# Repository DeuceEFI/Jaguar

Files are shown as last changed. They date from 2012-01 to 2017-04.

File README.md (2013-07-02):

# Jaguar Board for FreeEMS

JAG 07/02/2013 1157 EDT (GMT-0400)

####Do NOT use these files in the dev branch to make a PCB, the 0.6-alpha PCB has not been tested.  See the TODO.md file for the up to date changes from the 0.4-alpha to the 0.6-alpha board.  The 0.5-alpha was a commit of gerber files after I noticed that the traces were incorrect to the AAP and MAP sensors, it was never manufactured.

### Introduction

The name "Jaguar" comes from my initials and the great cat, keeping in the FreeEMS tradition of using cat names for hardware...  The aim of the Jaguar project is to create a hardware solution for FreeEMS that caters to the needs of the General Motors 4/6/8 cylinder engines running either an electronic advance distributor or wasted spark DIS system.  The Jaguar board can also be used for other 4/6/8 cylinder engines using a Ford EDIS ignition system.  The TC442xA Ignitor Drivers specified in the Bill of Materials can be used as logic level outputs to the logic level inputs on EDIS/DIS modules or to directly drive 12v ignitors. 

Please see forum.diyefi.org for the most up to date information and links for this project and all of the other aspects of the FreeEMS project.

### Goals

Core IO specs:

 * 1 FTDI USB (bus powered) communications (USB-B or USB-B-mini connector).
 * 2 RPM/Position VR or Hall/Opto/Digital inputs (ie: GM DIS Crankshaft 2x/3x/4x and 1x camshaft position sensor, CAM indicates cylinder #1).
 * 9 Standard 'CORE' analog inputs (IAT,MAT,CHT,TPS,O2,BRV,MAF,AAP,MAP).
 * 8 Available Port P PWM ports (PP0-7).
 * 8 Available Port B ports (PB0-7).
 * 2 Available Port K ports (PK4-5).
 * 4 ignitor 5v or 12v output channels, which can be used for:
   * Ignition advance output to GM DIS/GM HEI/Ford EDIS module.
   * DIS Bypass signal output to GM DIS/HEI module.
   * COP or CNP sequential ignition for 4 cylinder engines.
   * Wasted Spark ignition for 4, 6 or 8 cylinder engines.
 * 8 injector drivers (HI-Z ONLY 6A MAX per injector). Can setup to run 2 injectors from one CPU output using Port T4,5,6,7 or 1 injector per CPU output using Port B0-7 once firmware is ready.
 * 6 Ground connections (CPU, Injectors, Ignition, TPS, O2 Sensor and Analog Sensors).
 * 2 "12V" connections (Both are to be +12V SWITCHED, please use relay(s) to supply power to these pins).
 * 1 Fuel Pump relay low side driver.
 * 1 Cooling Fan relay low side driver.
 * 1 Accessory relay low side driver (Boost/Idle/TCC Lockup).
 * 1 switched +5V output for TPS.

PCB size is to be as small as possible, due to the limited room in the car (1932 Ford 5-Window Coupe) it is being designed for where space is a premium.  The goal is for a 3" x 5" (76mm x 127mm) PCB.  It is a mixture of SMD and through hole components so that it can be completed by a hobbyist with access to a DIY reflow soldering oven for the SMD work and a good soldering station for the through hole components.  The SMD components are all on the same side of the PCB, the through hole components are on the opposite side of the PCB.  With patience and a steady hand, all the SMD components can be hand soldered.

Case suggested is made by Context Engineering Co. and is made from extruded aluminum.  The part number for the case is 3008F-5N (flanged ends) and it is made for the Jaguar 3" x 5" PCB and is 1.85" tall overall.  Their website is http://www.contextengineering.com, there is a link in the BOM to purchase the case from a retailer. 

The suggested connectors are TE Connectivity (www.te.com) Automotive Grade water resistant connectors. 
All 35 positions on the connector are used for inputs/outputs when using all 8 injector drivers and all 3 relay drivers.

Connector Part #'s:

1-776163-2 Right Angle 35 Position Header (Natural Color)
The Jaguar Connector Board is design for any of the 1-776163-x Right Angle Headers.
I may also add a connector board design for the 1-776231-2 Vertical 35 Position Header (Natural Color) in the future.

AND you will need the following:
776164-2 35 Position AMP SEAL Plug Assembly (Natural Color)
770853-3 AMP SEAL Gold Plated Contact (order 40)
770678-1 AMP SEAL Seal Plug (for unused positions if you remove any from the connector, order 10)
 
### Status

For the most up to date status information for the project, refer to the TODO.md file which is maintained in sync with the schematics by a small team who verify each other's work.

### Changes

Please send any changes that you make to Jaguar back upstream to Andy Goss' copy at https://github.com/DeuceEFI/Jaguar

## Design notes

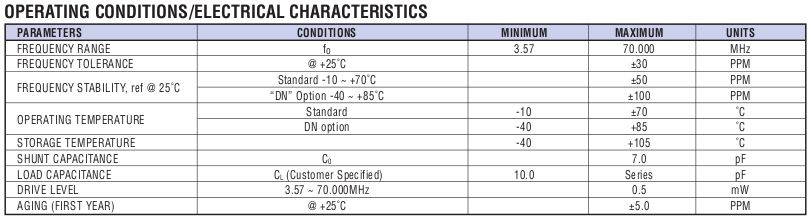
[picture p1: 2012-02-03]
docs/Crystal-Specs.png

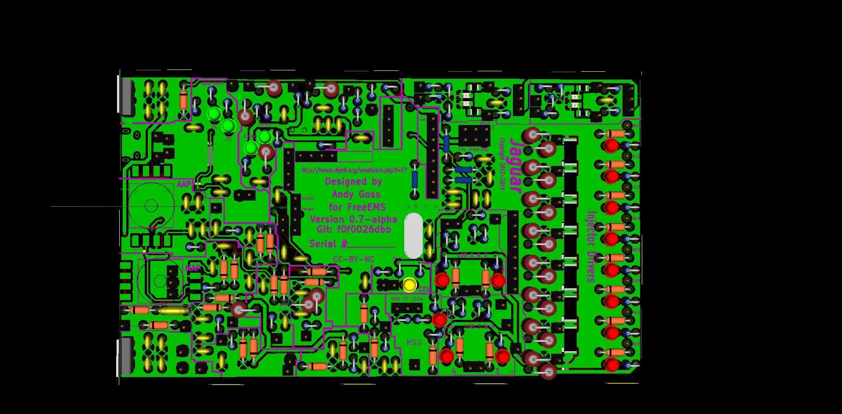
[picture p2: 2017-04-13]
docs/Jaguar-0.7-alpha-TH-Side.png

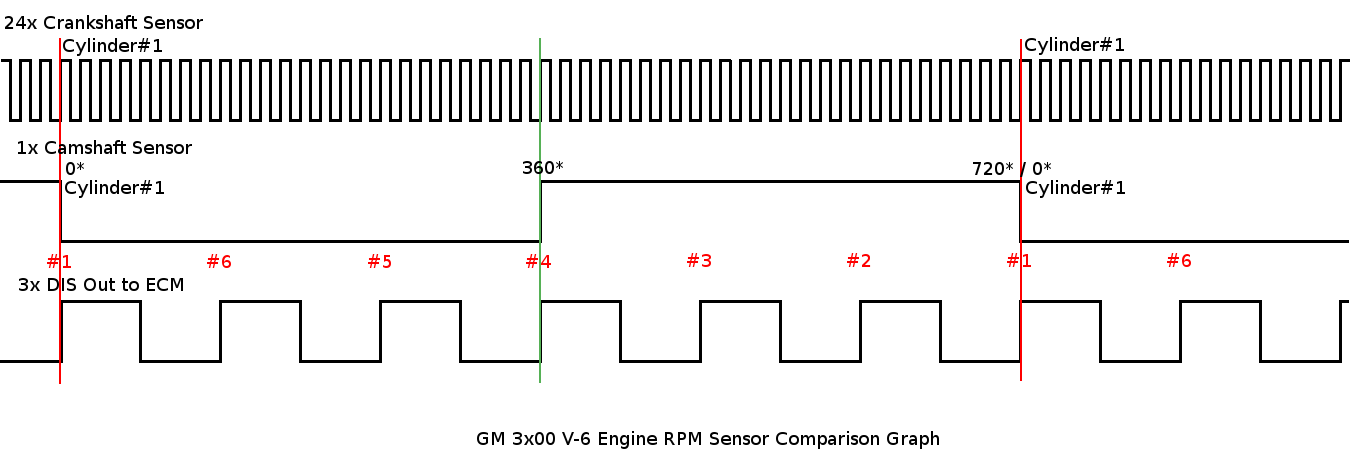
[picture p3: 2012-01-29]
docs/Crank-Cam-DIS-Waveforms.png

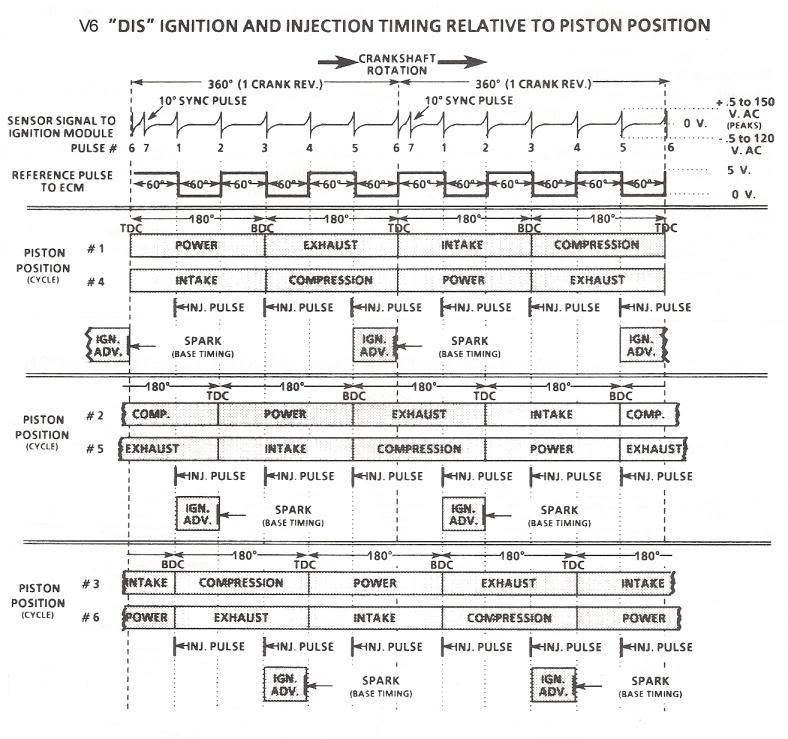
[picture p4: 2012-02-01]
docs/v6_dis.png

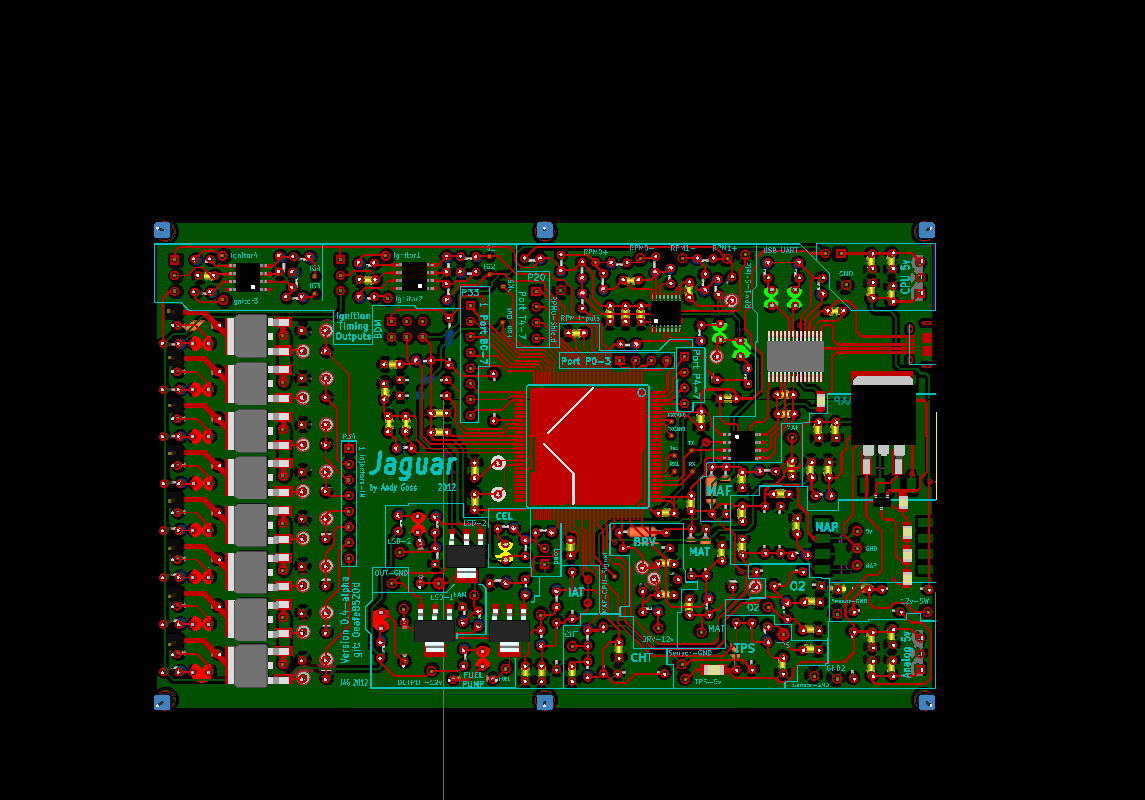
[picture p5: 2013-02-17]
docs/Jaguar-6MountingHoles.png

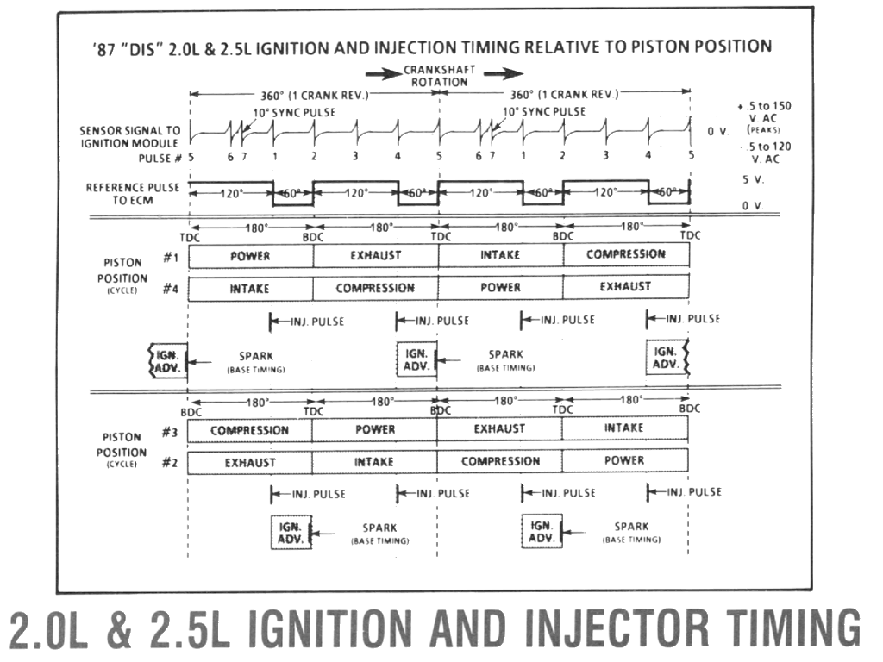
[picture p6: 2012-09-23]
docs/4cyl-DISinj-timing.gif

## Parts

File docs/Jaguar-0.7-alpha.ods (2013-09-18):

QTY | Reference | Value | Type | Information | To Order | CTM QTY | Manufacturer | Model# | Digikey P/N | Each | Order AMT | CTM | Note
 | Capacitors |  |  |  | 4
4 | C12,13,47,48 | 10uF | TANTALUM 10UF 35V 10% RADIAL, 0.098” LS | Tantalum | 16 | 4 | AVX Corporation | TAP106K035SCS | 478-1842-ND (http://www.digikey.com/product-detail/en/TAP106K035SCS/478-1842-ND/563945) | $1.62 | $25.92 | $6.48
13 | C1,2,3,4,5,8,20,27,37,38,44,51,55 | 0.22uF | CERAMIC 0.22UF 50V 10% RADIAL,X7R 0.098 LS | X7R | 52 | 13 | Kemet | C320C224K5R5TA | 399-4288-ND | $0.46 | $23.87 | $5.97
17 | C6,14,15,16,17,22,26,28,29,32,33,34,35,39,41,49,54 | 0.1uF / 100nF | CERAMIC 0.1UF 50V 10% RADIAL, 0.100” LS | X7R | 68 | 17 | Kemet | C320C104M1U5TA | 399-4264-ND | $0.22 | $15.23 | $3.81
1 | C7 | 6.8nF | CERAMIC 0.068UF 50V 5% RADIAL, 0.098” LS | C0G,NP0 | 4 | 1 | TDK Corportation | FK16C0G1H683J | 445-8330-ND | $0.76 | $3.04 | $0.76
1 | C9 | 680pF | CERAMIC 680PF 100V 5% RADIAL, 0.100” LS | C0G,NP0 | 4 | 1 | Kemet | C315C681J1G5TA | 399-4191-ND | $0.47 | $1.88 | $0.47
2 | C10,11 | 20pF | CERAMIC 20PF 100V 5% RADIAL, 0.100” LS | C0G,NP0 | 8 | 2 | AVX Corporation | SR151A200JAR | 478-7724-ND | $0.46 | $3.68 | $0.92
2 | C18,19 | 47uF | TANTALUM 47UF 10V 10% RADIAL, 0.100” LS | Tantalum | 8 | 2 | AVX Corporation | TAP476K010SCS | 478-1910-ND (http://search.digikey.com/us/en/products/TAP476K010SCS/478-1910-ND/564013) | $1.65 | $13.20 | $3.30
2 | C21,56 | 0.33uF | CERAMIC 0.33UF 50V 10% RADIAL, 0.100” LS | X7R | 8 | 2 | TDK Corporation | FK14X7R1H334K | 445-5312-ND (http://search.digikey.com/us/en/products/FK14X7R1H334K/445-5312-ND/2256792) | $0.38 | $3.04 | $0.76
3 | C23,42,53 | 0.01uF | CERAMIC 10000PF 50V 10% RADIAL, 0.100” LS | X7R | 12 | 3 | Kemet | C315C103K5R5TA | 399-4148-ND (http://www.digikey.com/product-detail/en/C315C103K5R5TA/399-4148-ND/817924) | $0.31 | $3.72 | $0.93
2 | C24,25 | 1nF | CERAMIC 1000PF 100V 10% RADIAL, 0.100” LS | X7R | 8 | 2 | Kemet | C315C102K1R5TA | 399-4144-ND (http://www.digikey.com/product-detail/en/C315C102K1R5TA/399-4144-ND/817920) | $0.32 | $2.56 | $0.64
6 | C30,31,36,43,52,57 | 1uF | CERAMIC 1UF 25V 10% RADIAL, 0.100” LS | X7R | 24 | 6 | Kemet | C315C105K3R5TA | 399-9714-ND | $0.79 | $18.96 | $4.74
1 | C40 | 4.7uF | TANTALUM 4.7UF 10V 10% RADIAL, 0.098” LS | Tantalum | 4 | 1 | AVX Corporation | TAP475K010SCS | 478-1903-ND (http://search.digikey.com/us/en/products/TAP475K010SCS/478-1903-ND/564006) | $0.63 | $2.52 | $0.63
 | Diodes/LEDs
1 | D1 (CEL) | LED-Yellow | LED SS 3MM 588NM YELLOW DIFF | 3mm-LED | 4 | 1 | Kingbright Corp | WP132XYD | 754-1212-ND (http://search.digikey.com/us/en/products/WP132XYD/754-1212-ND/1747611) | $0.15 | $0.60 | $0.15
1 | D2 | 5.6v 1w | DIODE ZENER 5.6V 3W AXIAL | DO-41 | 1 | 1 | ON Semiconductor | 1N5919BG | 1N5919BGOS-ND | $0.34 | $0.34 | $0.34
4 | D4,5,33,34 | LED-Green | LED SS 3MM 568NM GREEN DIFF | 3mm-LED | 16 | 4 | Kingbright Corp | WP132XGD | 754-1210-ND (http://search.digikey.com/us/en/products/WP132XGD/754-1210-ND/1747609) | $0.14 | $2.24 | $0.56
18 | D6,7,8,9,10,11,12,13,14,15,16,17,43,44,45,46,47,48 | 1N5818-TP | DIODE SCHOTTKY 1A 30V DO41 | DO-41 | 72 | 18 | Micro Commercial Co | 1N5818-TP | 1N5818-TPCT-ND (http://search.digikey.com/us/en/products/1N5818-TP/1N5818-TPCT-ND/950587) | $0.30 | $21.60 | $5.40
11 | D18,19,20,21,22,23,30,35,36,39,41 | LED-Red | LED SS 3MM 625NM RED DIFF | 3mm-LED | 44 | 11 | Kingbright Corp | WP132XID | 754-1211-ND (http://search.digikey.com/us/en/products/WP132XID/754-1211-ND/1747610) | $0.10 | $4.58 | $1.14
7 | D24,25,26,27,28,29,31,37,38,40,42 | 1N4148TA | DIODE SS FAST 100V 200MA DO35 | DO-35 | 28 | 7 | Fairchild Semiconductor | 1N4148TA | 1N4148TACT-ND (http://search.digikey.com/us/en/products/1N4148TA/1N4148TACT-ND/1532747) | $0.06 | $1.62 | $0.41
 | Connectors/Jacks
1 | J1 | USB-B micro | CONN USB MICRO B RECPT SMT R/A |  | 4 | 1 | FCI | 10118194-0001LF | 609-4618-1-ND | $0.43 | $1.73 | $0.43
1 | PLUG | TE Connectivity Plug | Automotive Connectors 35 POS AMP SEAL PLUG | Mouser | 0 | 1 | TE Connectivity/AMP | 1-776231-2 | 1-776231-2 (http://www.mouser.com/ProductDetail/TE-Connectivity-AMP/1-776231-2/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) | $14.00 | $0.00 | $14.00
1 | J3 | TE Connectivity Header | Automotive Connectors 35P AMPSEAL HDR ASSM NAT | Mouser | 0 | 1 | TE Connectivity/AMP | 1-7766163-2 | 1-776163-2 (http://www.mouser.com/ProductDetail/TE-Connectivity-AMP/1-776163-2/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) | $11.46 | $0.00 | $11.46
40 | Contacts for PLUG | TE Connectivity Contacts | Automotive Connectors AMPSEAL CONTACT | Mouser | 0 | 40 | TE Connectivity/AMP | 770854-3 | 770854-3 (http://www.mouser.com/ProductDetail/TE-Connectivity/770854-3/?qs=VZ9FDhhp7Snbed9QfbsDdg%3D%3D) | $0.68 | $0.00 | $27.20
10 | Seal Plug for Used Positions | TE Connectivity Seal Plug | AMPSEAL Accessory: SEAL PLUG | Mouser | 0 | 10 | TE Connectivity/AMP | 770678-1 | 770678-1 (http://www.mouser.com/ProductDetail/TE-Connectivity/770678-1/?qs=bVE8zYB%2Fq2c7eY42IkyCvQ%3D%3D) | $0.22 | $0.00 | $2.20
1 | MOV1 | Surge Protection | SURGE ABSORBER 14MM 22V 1000A ZNR | Disc 14mm | 4 | 1 | Panasonic - ECG | ERZ-V14D220 | P7307-ND (http://search.digikey.com/us/en/products/ERZ-V14D220/P7307-ND/227567) | $0.72 | $2.88 | $0.72
2 | F1,F2 | 8v/0.5A Polyfuse | PTC RESTTBLE 0.50A 8V CHIP 1206 | 1206 SMD | 8 | 2 | Bel Fuse Inc | 0ZCA0050FF2G | 507-1480-1-ND | $0.20 | $1.60 | $0.40
1 | L1 | 40 | Ferrite 1.5A 40 Ohm 0805 SMD | 0805 SMD | 4 | 1 | Laird-Signal Integrity Products | MI0805K400R-10 | 240-2389-1-ND | $0.10 | $0.40 | $0.10
2 | JP3,4,5,6,7,8,9 | Jumper | RES 0.0 OHM 1.5W JUMP 2512 SMD | 2512 SMD | 7 | 7 | Vishay Dale | CRCW25120000Z0EGHP | 541-0.0RBCT-ND | $1.58 | $11.07 | $3.16
 | Pin Headers
1 | Load1,P20,P21,P33,P34,JP1,JP2,JP10,JP11,JP16,PP1,PP2 | 0.100 Pin Header | CONN HEADER 50POS .100" SINGLE GOLD |  | 0 | 1 | Samtec Inc | TSW-150-07-L-S | SAM1031-50-ND (http://search.digikey.com/us/en/products/TSW-150-07-L-S/SAM1031-50-ND/1101377) | $3.11 | $0.00 | $3.11
1 | BDM 3x2 0.100” Pin Header | Two Row 0.100 Pin Header | CONN HEADER 34POS .100" DUAL GOLD |  | 0 | 1 | Samtec Inc | TSW-117-07-L-D | TSW-117-07-L-D-ND (http://search.digikey.com/us/en/products/TSW-117-07-L-D/TSW-117-07-L-D-ND/2796113) | $2.13 | $0.00 | $2.13
 | MOSFETs
8 | Q1,2,3,4,5,6,7,8 | VND7NV04 | MOSFET N-CH 40V 6A VND7NV04 60mOhm | DPAK | 0 | 8 | STMicroelectronics | VND7NV04 | 497-2669-5-ND (http://search.digikey.com/us/en/products/VND7NV04/497-2669-5-ND/603694) | $1.71 | $0.00 | $13.68
3 | Q9,10,11 | VNN7NV0413TR | MOSFET N-CH 40V 6A VNN7NV0413TR 60mOhm | SOT-223 | 0 | 3 | STMicroelectronics | VNN7NV0413TR | 497-2519-1-ND (http://search.digikey.com/us/en/products/VNN7NV0413TR/497-2519-1-ND/603901) | $1.71 | $0.00 | $5.13
1 | Q12 | KSH127TF | TRANSISTOR PNP 100V 8A DPAK | DPAK | 4 | 1 | Fairchild Semiconductor | KSH127TF | KSH127TFCT-ND | $0.61 | $2.44 | $0.61
 | Resistors
7 | R1,2,3,4,5,11,12 | 10k | RES 10.0K OHM 1/4W 1% METAL FILM |  | 28 | 7 | Yageo | MFR-25FBF-10K0 | 10.0KXBK-ND (http://search.digikey.com/us/en/products/MFR-25FBF-10K0/10.0KXBK-ND/13219) | $0.08 | $2.30 | $0.57
4 | R16,17,18,19 | 10k | RES 10.0K OHM 1/2W 1% METAL FILM | If using VR inputs | 16 | 4 | Vishay/BC Components | SFR16S0001002FR500 | PPC10.0KXCT-ND (http://search.digikey.com/us/en/products/SFR16S0001002FR500/PPC10.0KXCT-ND/594695) | $0.23 | $3.68 | $0.92 | Only purchase if using VR inputs
1 | R6 | 3.3k | RES 3.3K OHM 1/4W 0.1% AXIAL |  | 4 | 1 | Yageo | MFP-25BRD52-3K3 | 3.3KADCT-ND | $0.55 | $2.20 | $0.55
29 | R7,13,16,17,18,19,21,22,41,42,43,44,45,46,54,70,71,74,77,78,80,81,83,84,87,88,95,104,105 | 1k | RES 1.00K OHM 1/4W 1% METAL FILM |  | 116 | 29 | Yageo | MFR-25FBF-1K00 | 1.00KXBK-ND (http://search.digikey.com/us/en/products/MFR-25FBF-1K00/1.00KXBK-ND/13011) | $0.06 | $6.59 | $1.65
15 | R8,9,10,47,48,49,50,51,52,53,55,66,67,72,75 | 2.4k | RES METAL FILM 2.40K OHM 1/4W 1% |  | 60 | 15 | Stackpole Electronics Inc | RNMF14FTC2K40 | S2.4KCACT-ND (http://search.digikey.com/us/en/products/RNMF14FTC2K40/S2.4KCACT-ND/2617482) | $0.10 | $5.70 | $1.43
9 | R26,27,28,32,33,34,57,58,82 | 470 | RES METAL FILM 1/4W 470 OHM 1% AXIAL |  | 36 | 9 | Stackpole Electronics Inc | RNF14FTD470R | RNF14FTD470RCT-ND | $0.11 | $3.78 | $0.95
2 | R20,23 | 5.1k | RES 5.1K OHM 2W 5% AXIAL | Not Needed for Hall | 8 | 2 | Yageo | FMP200JR-52-5K1 | 5.1KZCT-ND | $0.20 | $1.60 | $0.40 | Only purchase if using VR inputs
3 | R24,25,31 | For GM sensors | 2.49k | RES 2.49K OHM 0.25W 0.1% METAL FILM | For GM Sensors | 12 | 3 | TT Electronics/Welwyn | RC55Y-2K49BI | 985-1047-1-ND (http://search.digikey.com/us/en/products/RC55Y-2K49BI/985-1047-1-ND/2401912) | $1.92 | $23.04 | $5.76 | Only purchase if using GM Sensors
0 | R24,25,31 | For most sensors | 2.43k | RES 2.43K OHM 0.25W 0.1% METAL FILM | For Most Sensors | 0 | 0 | TT Electronics/Welwyn | RC55Y-2K43BI | 985-1046-1-ND (http://search.digikey.com/us/en/products/RC55Y-2K43BI/985-1046-1-ND/2401911) | $1.29 | $0.00 | $0.00 | Good compromise for most Sensors
0 | R24,25,31 | For Ford sensors | 27.4k | RES 27.4K OHM 0.25W 0.1% METAL FILM AXL | For Ford Sensors | 0 | 0 | TT Electronics/Welwyn | RC55Y-27K4BI | 985-1069-1-ND (http://search.digikey.com/us/en/products/RC55Y-27K4BI/985-1069-1-ND/2401934) | $1.29 | $0.00 | $0.00 | Only purchase if using Ford Sensors
0 | R24,25,31 | For MOPAR sensors | 9.1k | RES 9.1K OHM 1/4W 0.1% METAL FILM AXL | For MOPAR Sensors | 0 | 0 | Yageo | MFP-25BRD52-9K1 | 9.1KADCT-ND (http://search.digikey.com/us/en/products/MFP-25BRD52-9K1/9.1KADCT-ND/2059152) | $0.44 | $0.00 | $0.00 | Only purchase if using Mopar Sensors
1 | R29 | 3.9k | RES 3.9K OHM 1/4W 0.1% METAL FILM AXL |  | 4 | 1 | Yageo | MFP-25BRD52-3K9 | 3.9KADCT-ND (http://search.digikey.com/us/en/products/MFP-25BRD52-3K9/3.9KADCT-ND/2059137) | $0.55 | $2.20 | $0.55
1 | R30 | 1.0k | RES 1K OHM 1/4W 0.1% METAL FILM AXL |  | 4 | 1 | Yageo | MFP-25BRD52-1K | 1KADCT-ND (http://search.digikey.com/us/en/products/MFP-25BRD52-1K/1KADCT-ND/2059121) | $0.55 | $2.20 | $0.55
15 | R35,36,37,38,39,40,63,68,69,73,76,89,90,102,103 | 100k | RES 100K OHM 1/4W 1% METAL FILM |  | 60 | 15 | Yageo | MFR-25FBF-100K | 100KXBK-ND (http://search.digikey.com/us/en/products/MFR-25FBF-100K/100KXBK-ND/13473) | $0.06 | $3.41 | $0.85
4 | R91,92,100,101 | 160 | RES 160 OHM 2W 1% AXIAL |  | 16 | 4 | Yageo | FMP200FRF52-160R | 160YCT-ND | $0.27 | $4.32 | $1.08
2 | R106,107 | 10k | RES 10K OHM 1/8W 0.1% 0805 SMD | 0805 SMD | 8 | 2 | Bourns Inc | CRT0805-BY-1002ELF | CRT0805-BY-1002ELFCT-ND | $0.51 | $4.08 | $1.02
1 | R108 | 330 | RES 330 OHM 1/8W 0.1% 0805 SMD | 0805 SMD | 4 | 1 | Panasonic Electronic Components | ERA-6AEB331V | P330DACT-ND | $0.63 | $2.52 | $0.63
1 | R109 | 604 | RES 604 OHM 1/8W 0.1% 0805 SMD | 0805 SMD | 4 | 1 | Panasonic Electronic Components | ERA-6AEB6040V | P604DACT-ND | $0.63 | $2.52 | $0.63
 | ICs
1 | U1 | MC9S12XDP512 | IC MCU 512K FLASH 112-LQFP MC9S12XDP512MAL | LQFP-112 |  | 1 | Freescale Semiconductor | MC9S12XDP512MAL | MC9S12XDP512MAL-ND (http://search.digikey.com/us/en/products/MC9S12XDP512MAL/MC9S12XDP512MAL-ND/1167902) | $23.53 | $0.00 | $23.53
2 | U2,3 | LM2940T-5.0/NOPB | IC REGULATOR LDO LM2940-5.0 1A TO220 | TO-220 | 8 | 2 | Texas Instruments | LM2940T-5.0/NOPB | LM2940T-5.0/NOPB | $1.68 | $13.44 | $3.36
2 | U2,3 | SP900S-0.009-AC-54 | SILICONE THERMAL PAD TO-220 W/ADH .009" SP9 |  | 8 | 2 | Bergquist | SP900S-0.009-AC-54 | BER182-ND | $0.18 | $1.44 | $0.36
2 | U2,3 | 7721-7PPSG | INSULATING SHOULDER WASHER |  | 8 | 2 | Aavid Thermalloy | 7721-7PPSG | HS418-ND | $0.23 | $1.84 | $0.46
2 | U2,3 | 4724 | MICA PAD AND HARDWARE MOUNTING KIT FOR TO-220 |  | 8 | 2 | Keystone Electronics | 4724 | 4724K-ND | $1.94 | $15.52 | $3.88
1 | U4 | MAX9926UAEE+ | IC SENSOR INTERFACE VARI 16-QSOP | 16-QSOP | 4 | 1 | Maxim Integrated Products | MAX9926UAEE+ | MAX9926UAEE+-ND (http://search.digikey.com/us/en/products/MAX9926UAEE%2B/MAX9926UAEE%2B-ND/2062014) | $3.59 | $14.36 | $3.59
1 | U6 | MPXA4250AC6U | PRESSURE SENS 36.3PSI MAX 8-SOP | 8-SOIC | 0 | 1 | Freescale Semiconductor | MPXA4250AC6U | MPXA4250AC6U-ND | $16.37 | $0.00 | $16.37
1 | U7 | FT232RL | IC FT232RL USB FS SERIAL UART 28-SSOP | 28-SSOP | 4 | 1 | FTDI, Future Technology Devices International Ltd | FT232RL-REEL | 768-1007-1-ND (http://search.digikey.com/us/en/products/FT232RL-REEL/768-1007-1-ND/1836402) | $4.50 | $18.00 | $4.50
1 | U8 | ADUM3201BRZ | ISOLATOR DGTL 10MBPS 2CH 8SOIC | 8-SOIC | 4 | 1 | Analog Devices | ADUM3201BRZ | ADUM3201BRZ-ND | $3.63 | $14.52 | $3.63
2 | U9,12 | TC4427AEOA | IC MOSFET DVR 1.5A DUAL HS 8SOIC | 8-SOIC | 8 | 2 | Microchip Technology | TC4427AEOA | TC4427AEOA-ND | $1.24 | $9.92 | $2.48
1 | U11 | MPXA6115AC6U | PRESSURE SENS 16.7PSI MAX 8-SOP |  | 0 | 1 | Freescale Semiconductor | MPXA6115AC6U | MPXA6115AC6U-ND | $12.55 | $0.00 | $12.55
1 | U13 | TL431BQDBZR | IC VREF SHUNT PREC ADJ SOT-23-3 | SOT-23-3 | 4 | 1 | Texas Instruments | TL431BQDBZR | 296-17623-1-ND | $0.72 | $2.88 | $0.72
 | Crystal
1 | X1 | 16.0MHz | CRYSTAL 16.000 MHZ 20PF 49US -40C to 85C | HC-49US | 4 | 1 | ECS Inc | ECS-160-20-4DN | X192-ND (http://search.digikey.com/us/en/products/ECS-160-20-4DN/X192-ND/281763) | $1.12 | $4.48 | $1.12 | Recommended for current design
 |  |  |  |  |  |  |  | Cost To Manufacture (CTM) |  | US Dollars |  | $214.70 | Not including shipping or sales tax
1 | Case |  | 3.12”x5.00”x1.85” Extruded Aluminum Split Body Case |  |  | 1 | Context Engineering Company | 3008H-5B (plain ends) or 3008F-5N (flanged ends) | http://store01.prostores.com/servlet/thescienceshop/the-2220/5.0%22-L-x-3.12%22/Detail | $14.99 | $0.00 | $14.99
 | Printed Circuit Board
1 | Jaguar PCB | Estimate ONLY |  |  |  | 1 | N/A | N/A |  | $8.19 | $0.00 | $8.19 | 10 Prototype boards cost $81.90
 |  |  |  |  |  |  |  | Total of Materials:Cost to Manufacture |  | US Dollars |  | $237.88 | Not including shipping or sales tax
 |  |  |  |  |  |  |  |  | Order Total |  | $335.25
 |  |  |  |  |  |  |  |  |  |  |  | 278

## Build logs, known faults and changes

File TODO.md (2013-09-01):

# To Do List

## JAG 09/01/2013 0015 EDT (GMT-0400)

### Things left to change For Version 0.6-alpha PCB based on what has been learned from 0.4-alpha/0.5-alpha PCB:

* Add an additional 4" x 6" board design with TE Connectivity 35 position connector mounted to it instead being on a separate carrier board.
* Update Assembly documentation to reflect these changes for the Version 0.6-alpha PCB.

----------
### Jaguar Wish List Items:

* Add netlist "Label"s to connection wires on the schematics so they appear on the board layout and in the netlists.

----------
### 0.6-alpha Changes Completed:

* L1, R106, R107, R108, R109 and U13 silkscreens are not visible, ie: too small. - DONE 05/10/2013
* Increased RPM0+ wire hole diameter to the same as RPM0-. - DONE 05/10/2013
* Deleted R79 from the BOM, it has been replaced by L1. - DONE 05/10/2013
* Moved Injector Outputs lettering on component side away from INJ4-GND and INJ5-GND letterning. - DONE 05/10/2013
* Deleted D2 from PCB, it is not in the schematic any longer. - DONE 05/10/2013
* IAT silkscreen lettering on component side read TAT, moved IAT away from pad to correct. - DONE 05/10/2013
* Moved C2 silkscreen to one side, away from silkscreen line. - DONE 05/10/2013
* CEL circuit outline on component side was incomplete. Also added CEL text on component side. - DONE 05/10/2013
* Moved Jaguar by Andy Goss 2012-13 on component side to under FTDI IC, where there was more room. - DONE 05/10/2013
* 12v trace to MOV was too narrow and would burn while MOV active, made trace wider. - DONE 05/10/2013
* RPM0 and RPM1 LED silkscreen labels were reversed. - DONE 05/10/2013
* Changed Load/Run label to Load. - DONE 05/11/2013
* Low side driver diodes were not labeled correctly, it had partial part number rather than component ID. - DONE 05/11/2013
* Added low side driver separating lines on the PCB silkscreen to show the separation of the FP and LSD-1. - DONE 05/12/2013
* Made Silkscreen area separating lines wider. - DONE 05/12/2013
* R20 and R23 footprints were too small for 3w resistor, used bigger footprint and moved other components out of the way. - DONE 05/12/2013
* Renamed PK5 to PortK5. - DONE 05/13/2013
* Renamed FAN-OUT to PortK4. - DONE 05/13/2013
* Renamed ACC to LSD-2, rename ACC- to LSD2-. - DONE 05/13/2013
* Renamed FAN to LSD-1, rename FAN- to LSD1-. - DONE 05/13/2013
* Renamed OUT-GND to OUTPUT-GND. - DONE 05/13/2013
* Renamed MAT to SPR. - DONE 05/13/2013
* Added a pair of mica T0-220 isolator kits to the BOM to isolate the voltage regulators from the case. - DONE 05/13/2013
* Renamed OUTPUT-12v to IGN-12v as it wasn't clear what this pad was for. - DONE 05/13/2013
* Renamed LSD2- to LSD2, renamed LSD-2 to LSD2-IN, renamed FAN- to LSD1, renamed FAN to LSD1-IN, renamed FUEL- to FUEL. - DONE 05/14/2013
* Added 5.6v zener diode to output of CPU 5v filtering capacitors to clamp voltage spikes. - DONE 05/15/2013
* IG1, IG2, IG3 and IG4 pads/holes increased from 0.0215" to 0.0315" diameter. - DONE 05/16/2013
* Renamed PortK5 to PK5 to conserve space. - DONE 05/21/2013
* Renamed PortK4 to PK4 to conserve space. - DONE 05/21/2013
* Made BDM pad spacing 0.100" and hole diameter 0.0315", which is similar to the spacing for C42, C26 and C43. - DONE 05/21/2013
* Changed the wording of Injector Outputs to Injector Drivers. - DONE 05/21/2013
* Changed the wording "by Andy Goss 2012-2013" under Jaguar to "Copyright 2012-2013". - DONE 05/21/2013
* Changed the wording "Andy Goss (DeuceEFI)" to "Andy Goss". - DONE 05/21/2013
* Removed the wording "2012-2013" that was after "for FreeEMS" in the center of the board. - DONE 05/21/2013
* Changed the wording of "Ignition Outputs" to "Ignition Outputs 1 & 2" and "Ignition Outputs 3 & 4". - DONE 05/21/2013
* Added INJ1, INJ2, INJ3, etc to the through hole component side of the PCB. - DONE 05/21/2013
* Changed Load pads to use a 0.0315" drill like the BDM pads for a snug fit so the header doesn't fall out. - DONE 05/21/2013
* Made the CANRX0/CANTX0 into a 0.100" header so that a add-on card could be created later. - DONE 05/21/2013
* Added a second fuse (F2) between stock MAP power supply pad and external through hole 5vdc connection point for the external MAP sensor. - DONE 05/21/2013
* I verified that the AAP 5vdc is not after the TPS protection fuse (F1) or F2. - DONE 05/21/2013
* Renamed RX to RX0 and TX to TX0 since there is RX1/TX1 already marked. - DONE 05/24/2013
* Changed R20 and R23 (VR shunt resistors) from 5k to 5.1k due to 2W package availability. - DONE 05/24/2013
* Changed RX0/TX0 to a 0.100" 2-pin header for those that want to experiment with TTL serial devices other than the FTDI USB IC. - DONE 05/24/2013
* Changed R91,92,100,101 from 150 ohm 1/2W to 160 ohm 2W resistors. - DONE 06/09/2013
* Changed 1uF capacitors to be 0.100" lead spacing in BOM. - DONE 07/02/2013
* Changed R6 3.3k ohm resistor to be a 0.094" Dia x 0.248" Long body in BOM. - DONE 07/02/2013
* Noted on the shematic that there are missing component IDs that do not exist due to design changes. - DONE 07/19/2013
* Added vias from ground plane under MCU to the ground plane on the bottom of the PCB. - DONE 07/30/2013
* Corrected footprints for the adjustable zener (U13) and the PNP transistor (Q12) as they are numbered differently by the manufacturer compared to the KiCAD footprints for SOT-23-3 and SOT-223 components and then re-route traces to these components. - DONE 08/26/2013
* Replaced the LM2937EM-5.0 0.5A low dropout voltage regulators with LM2940T-5.0 1.0A low dropout voltage regulators. - DONE 08/31/2013
* Changed the 5v feeds to the MAX9926 and the TC442xA ICs to be from the CPU-5v power supply rather than the Analog-5v power supply. - DONE 08/31/2013
* Increased all 5v power supply traces from 0.150" to 0.350", except where they connect to IC solder pads. - DONE 09/01/2013

----------
### 0.5-alpha Changes Completed:
Note: This board was never manufactured, but it is tagged in my repository.

* Corrected AAP and MAP Sensor Footprints and re-ran traces to correct pads. - DONE 04/08/2013
* Updated Bill of Materials (BOM) after adding the 5vdc Analog Power Supply Protection circuit. - DONE 05/10/2013

----------
### 0.4-alpha Changes Completed:

* Fix R12 and C1 pads from being connected to the ground plane on the Through Hole component side - DONE 03/2012
* Delete JP6 (not necessary) - DONE 04/15/2012
* Change XOR chip from DIP to SMD - Changed Footprint, still need to regenerate PCB file - DONE 05/13/2012 
* Make Silk Screen lines thinner for outlines on SMD side
* Move R15 label from inside XOR (U5) outline to outside near R15's position -DONE 07/04/2012
* Add D37, D38, D40 and D42 to BOM - DONE 04/14/2012
* Improve the silk screen for the LEDs to show anode/cathode orientation - DONE 07/04/2012
* Too much copper around pads, looks like it is set to 8 per hole, 4 would be better/sufficient/good - DONE 07/04/2012
* Along with #9 above, revisit ground plane thermal relief rules to keep from sucking all the heat out of the pad while soldering - DONE 05/13/2012 
* Increase Thermal Relief Antipad Size from 0.0200" to 0.0300", Copper Width from 0.0200" to 0.0150" -DONE 05/13/2012
* C26, C42 and C43 need to be different part #'s with different lead spacing or the footprint changed back to 3mm disc - DONE 07/05/2012
* Move C17 label outside of U3 - DONE 05/13/2012
* Delete D43 and D44 as the LM2937 is already reverse protected - DONE 04/15/2012
* Fix J2 footprint so that the pin out connections are correct - DONE 05/13/2012
* Re-route power feed to MOV first, then to the input capacitors, then to the regulators - DONE 07/04/2012
* Move FAN and FUEL labels and outlines to observe the 1/16" space from the edge of the PCB for the case slot - DONE 07/04/2012
* Re-route some of the ground plane traces onto the Through Hole side of the PCB to clean up the SMD side (signal side) - DONE 07/04/2012
* Add more space around the BDM header - DONE 07/04/2012
* Remove the 5.6v Zener diode (D3) as it is not necessary since there is no chance of voltage feeding back from the MCU - DONE 05/26/2012
* Add 1k resistor to each output of the MAX9926 to limit current to MCU Port T0 and T1 - DONE 05/26/2012
* Change 5vdc-analog to 5vdc-cpu at CEL (D1) so that the CPU supply is used to power up all the necessary MCU functions. (Analog supply should only be for inputs from the engine) - DONE 05/26/2012
* FTDI USB IC decouple caps are on the wrong side of the feed from R79, and also pretty far from the IC - DONE 07/04/2012
* Check MAX9926 decouple caps to make sure power feed is on the correct side and they are close to the IC - DONE 07/04/2102
* Check the MCU decouple caps are close to the MCU and power is feeding from the correct side - DONE 07/04/2012
* Label GND/RESET or something near BDM (possibly), might have to shift BDM over a little - DONE 07/04/2012
* C10 and C11 (crystal load capacitors) need to be changed to 20pF to match the manufacturer specifications. - DONE 05/26/2012
* Update BOM to use S912XDP512MAL MCU not the VAL variant as listed. (I used the MAL on all my prototypes). DONE 07/02/2012
* Add git hash to PCB design file for tracking - DONE 07/04/2012
* Update the Jaguar Assembly Manual with photos of the Serial #1 build. - DONE 07/05/2012
* Add instructions to use High Temperature Silicone or something similar to brace the upright components - DONE 07/05/2012
* Added MAF input protection circuit. - DONE 08/29/2012 
* Added RXCAN0 and TXCAN0 solder pads. - DONE 10/29/2012
* Added circuit borders to Through Hole side silkscreen. - DONE 10/29/2012
* Added an SMD AAP sensor for measuring the atmospheric pressure in addition to the changing the existing MAP sensor to an SMD sensor. - DONE 11/13/2012
* Changed R8 from 10k Ohm to 2.4k Ohm to be a stronger pull up to 5v. - DONE 02/16/2013
* 5V Analog Power Supply Protection. - DONE 02/16/2013
* Add additional board design that is wider with 3 mounting holes on down the long sides. - DONE 02/17/2013
* Separate USB connector shield from USB ground, per section 2.2.2 Grounds of http://www.ftdichip.com/Support/Documents/AppNotes/AN_146_USB_Hardware_Design_Guidelines_for_FTDI_ICs.pdf - DONE 02/19/2013
* Change 3mm bolt holes to have 6mm pads with 0.5mm spacing between pad and other trace. - DONE 02/19/2013
* Find a smaller package PNP for clamp circuit. I found an SOT-223 footprint Diodes Inc. part # ZXTP25020DGTA. -DONE 02/19/2013

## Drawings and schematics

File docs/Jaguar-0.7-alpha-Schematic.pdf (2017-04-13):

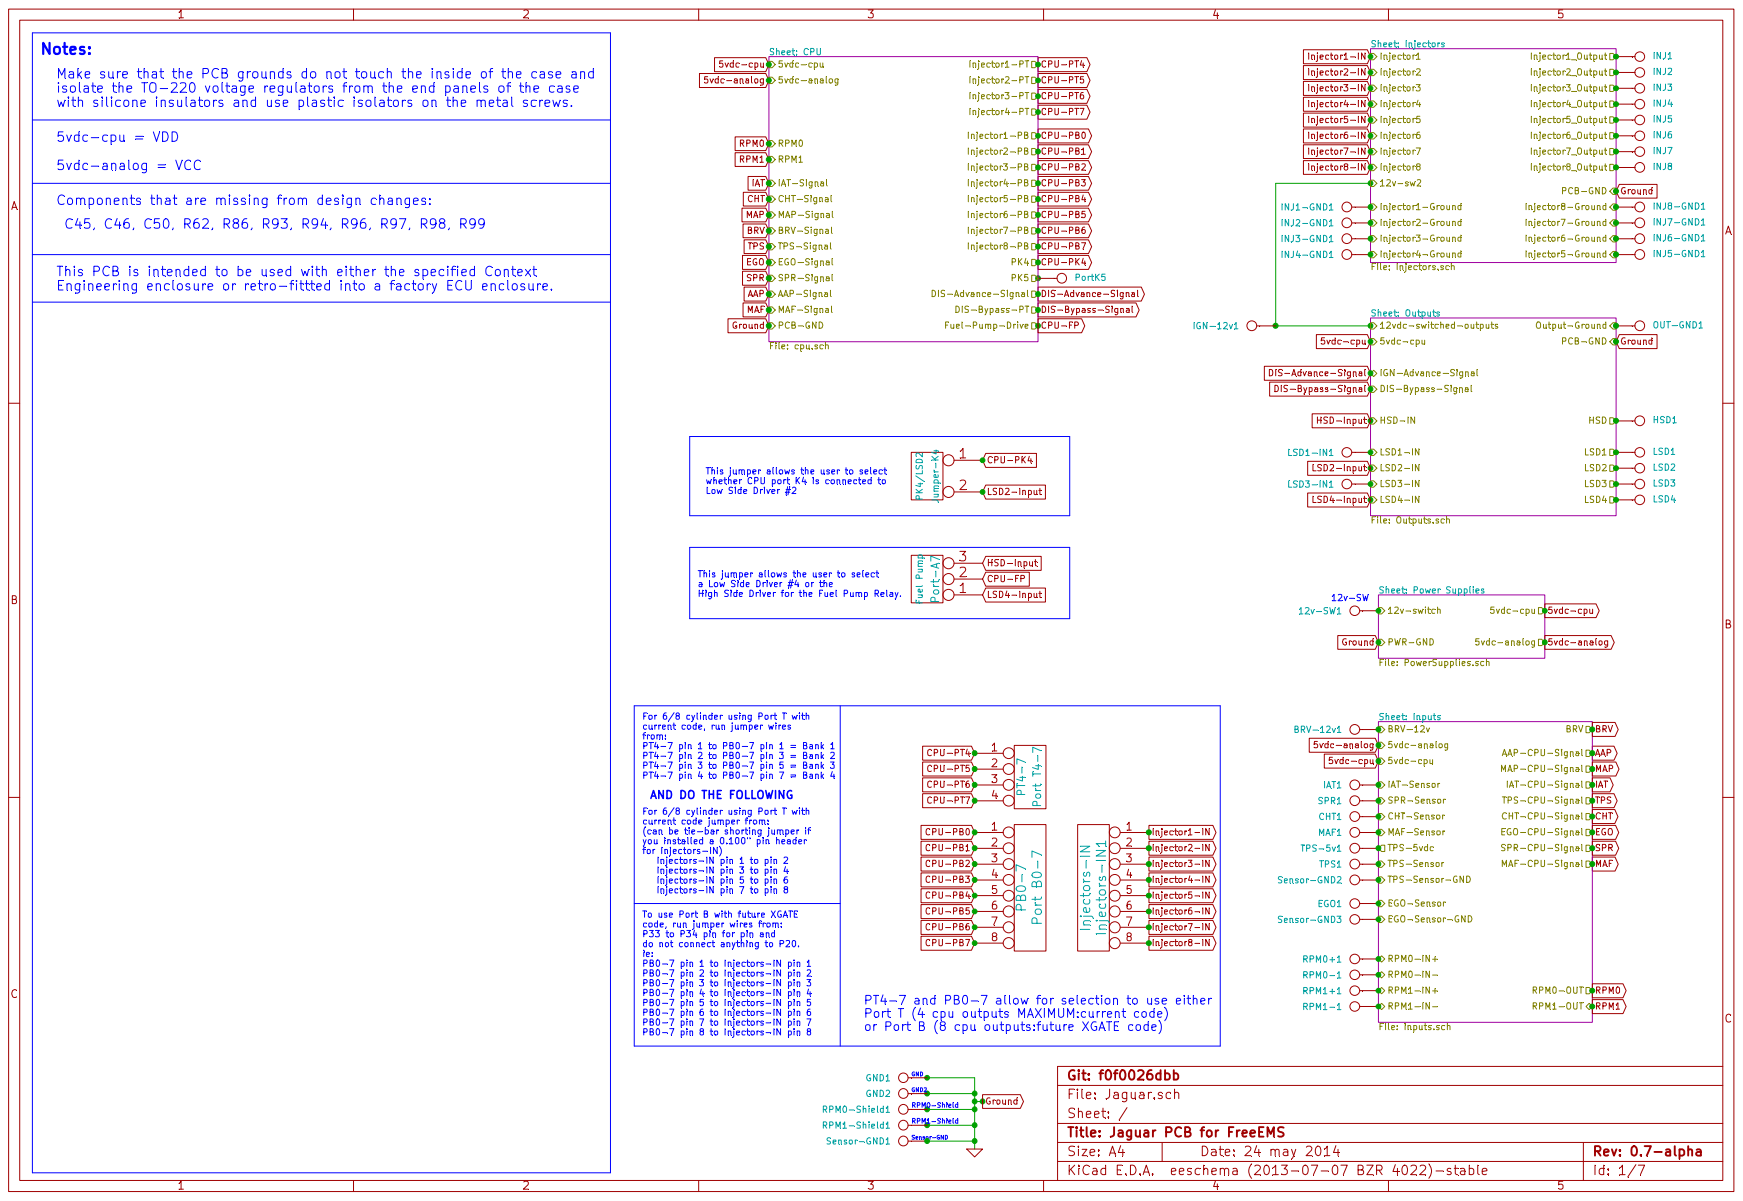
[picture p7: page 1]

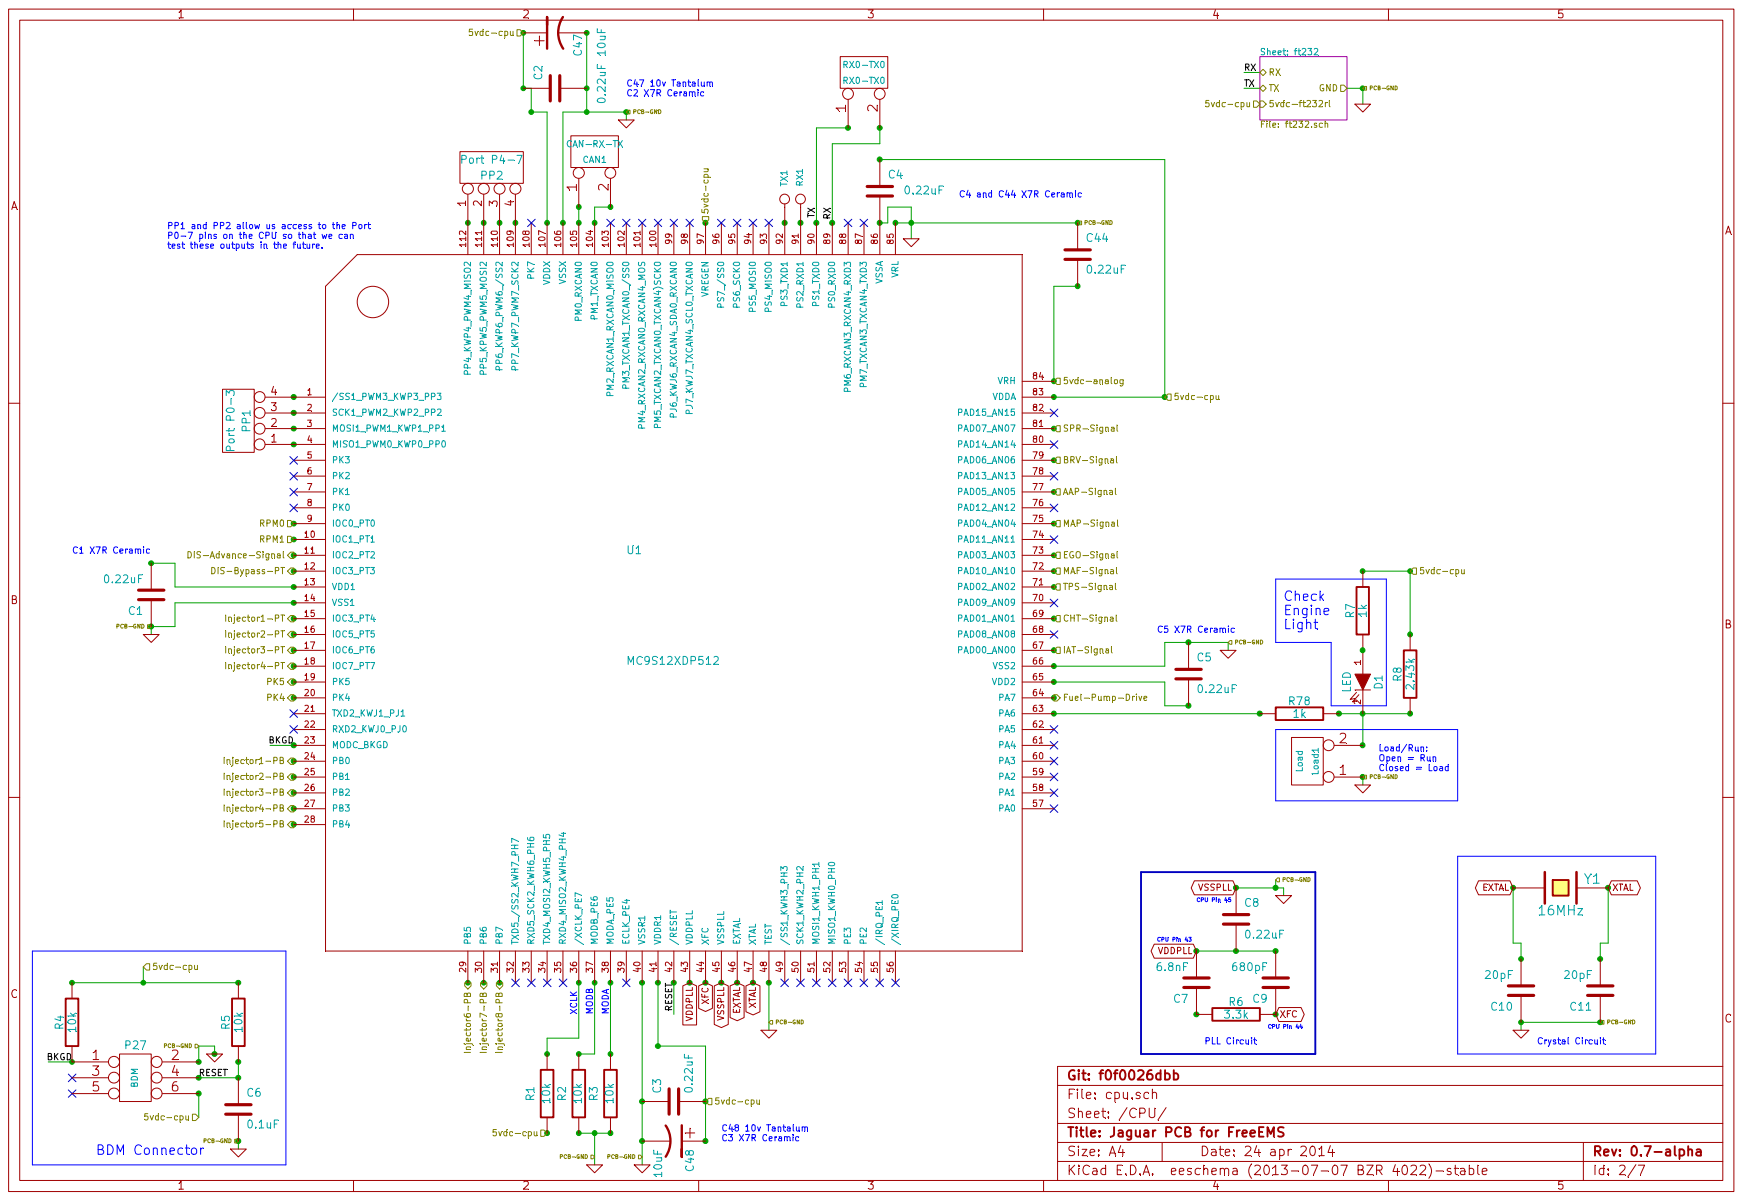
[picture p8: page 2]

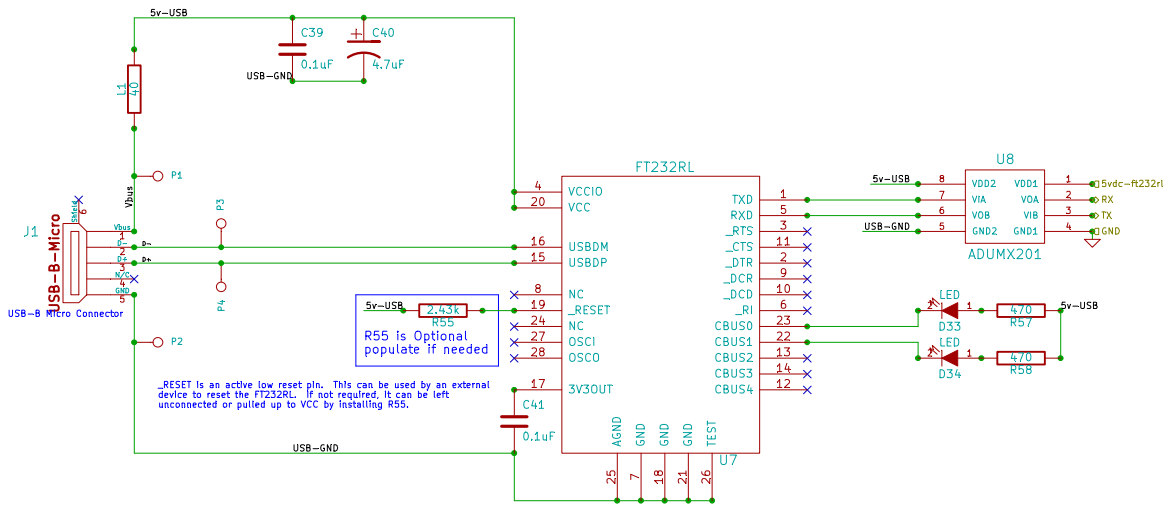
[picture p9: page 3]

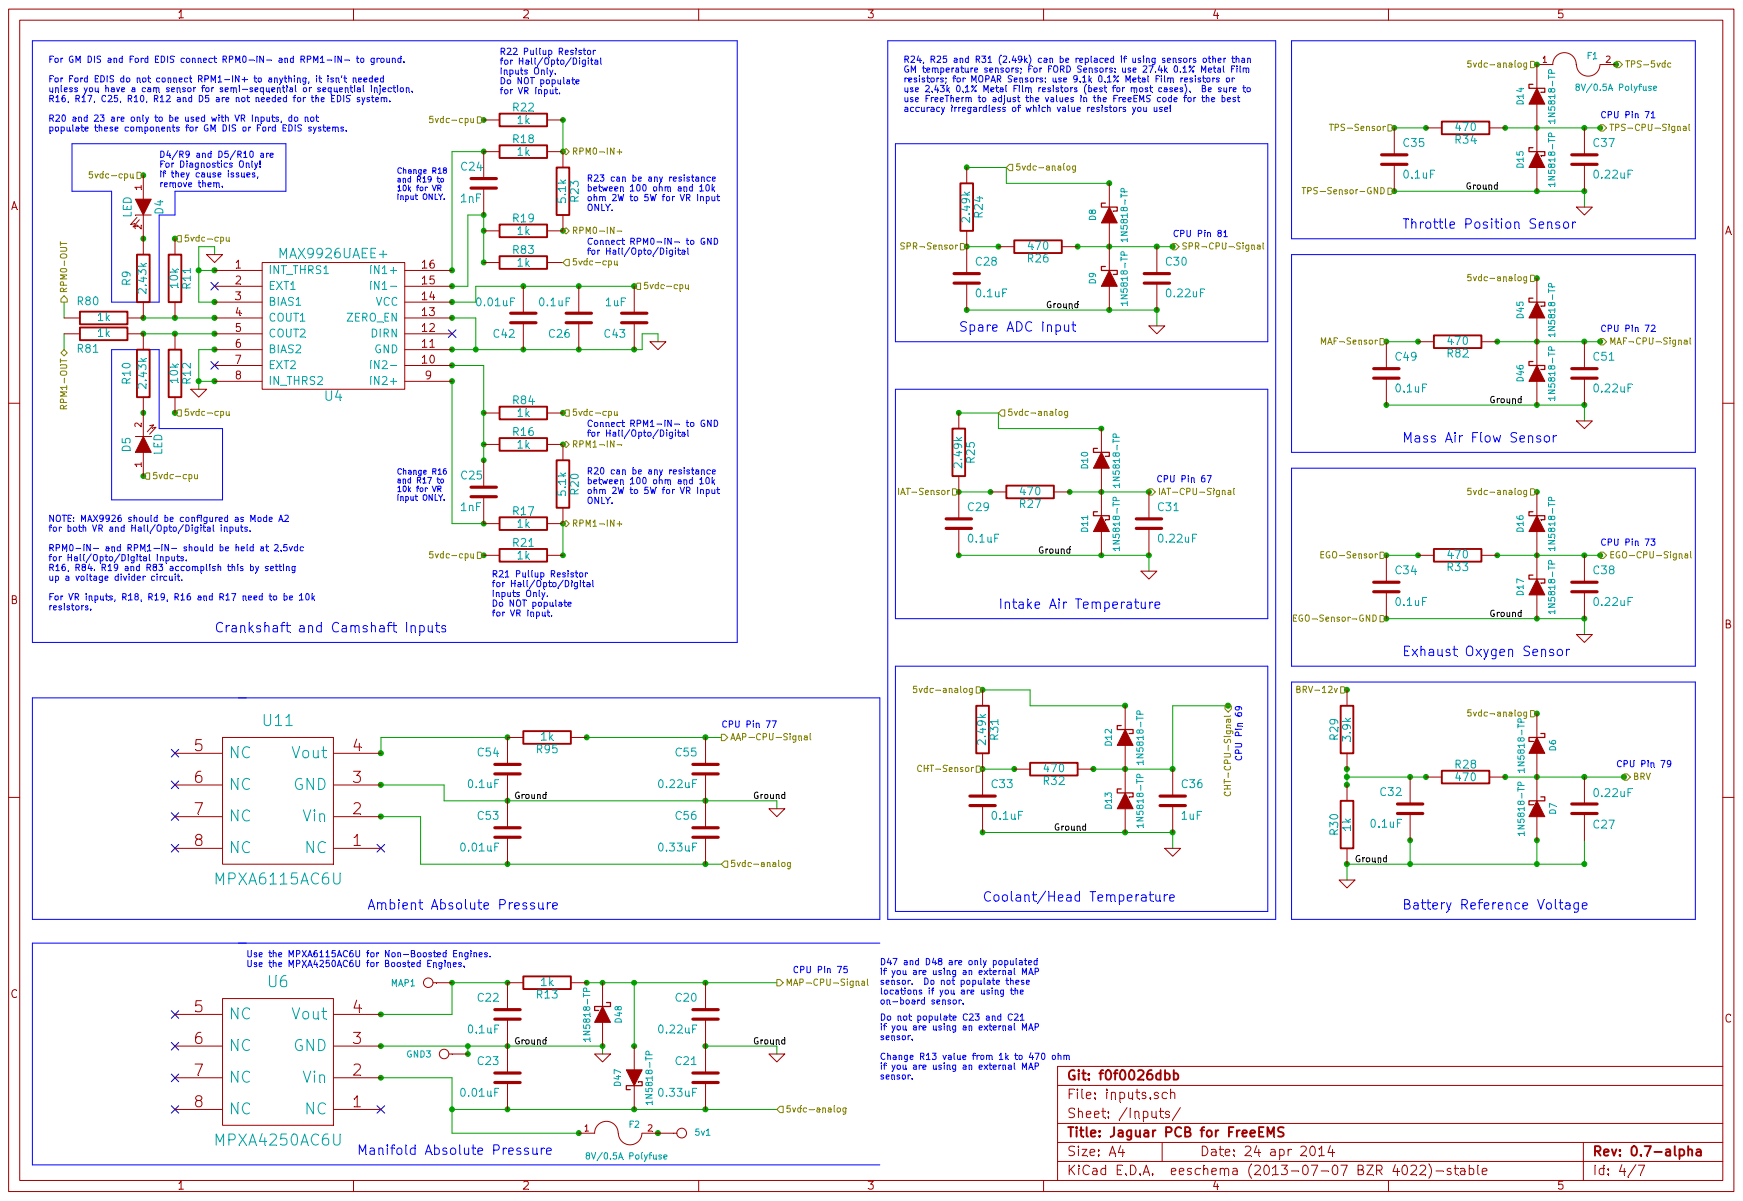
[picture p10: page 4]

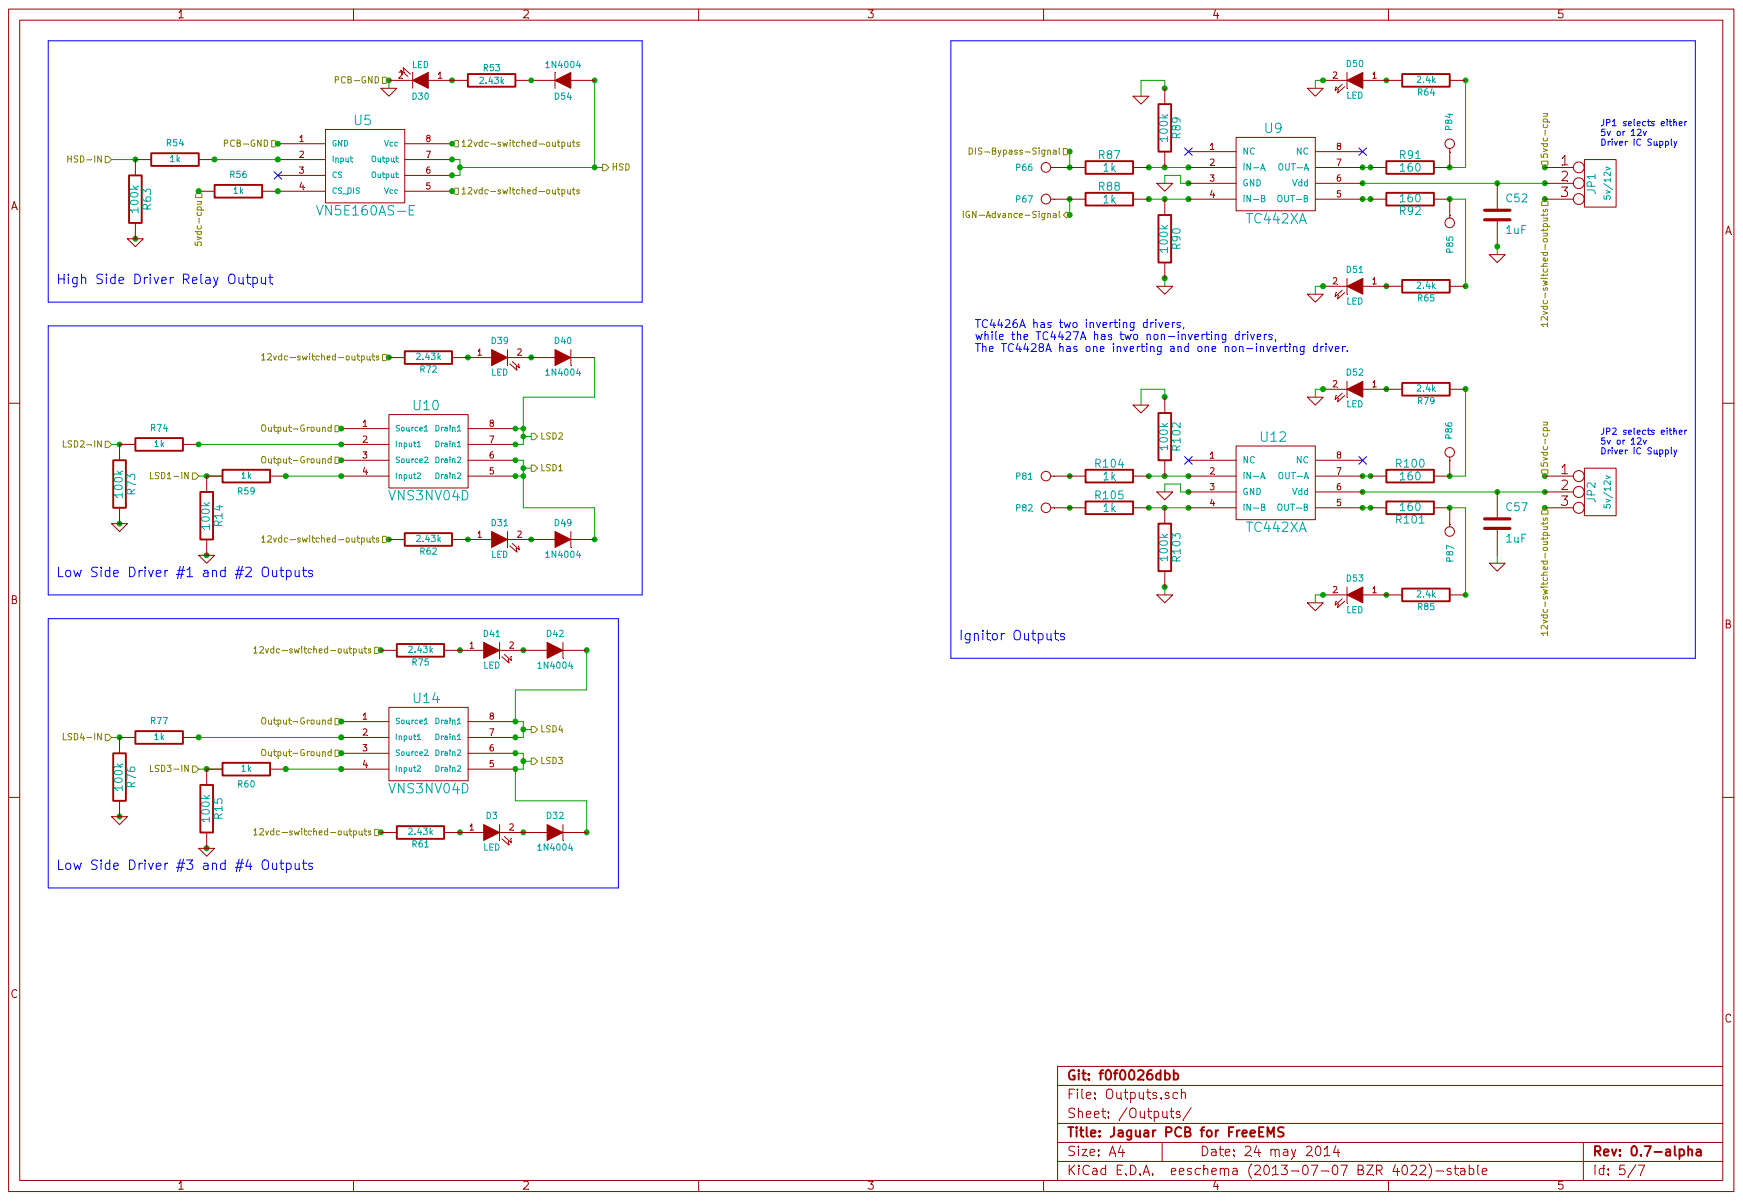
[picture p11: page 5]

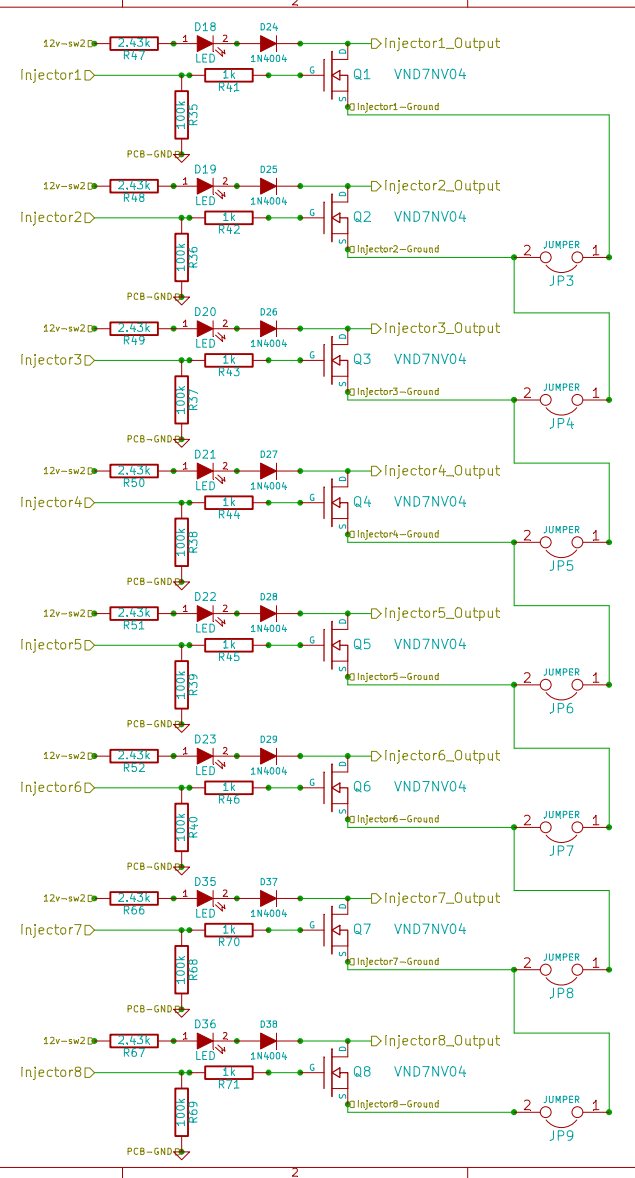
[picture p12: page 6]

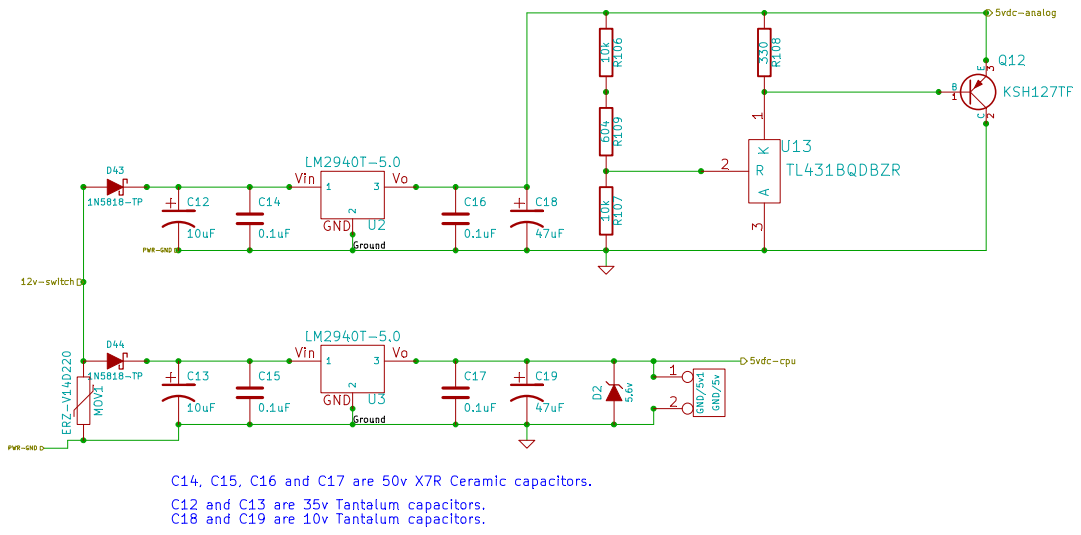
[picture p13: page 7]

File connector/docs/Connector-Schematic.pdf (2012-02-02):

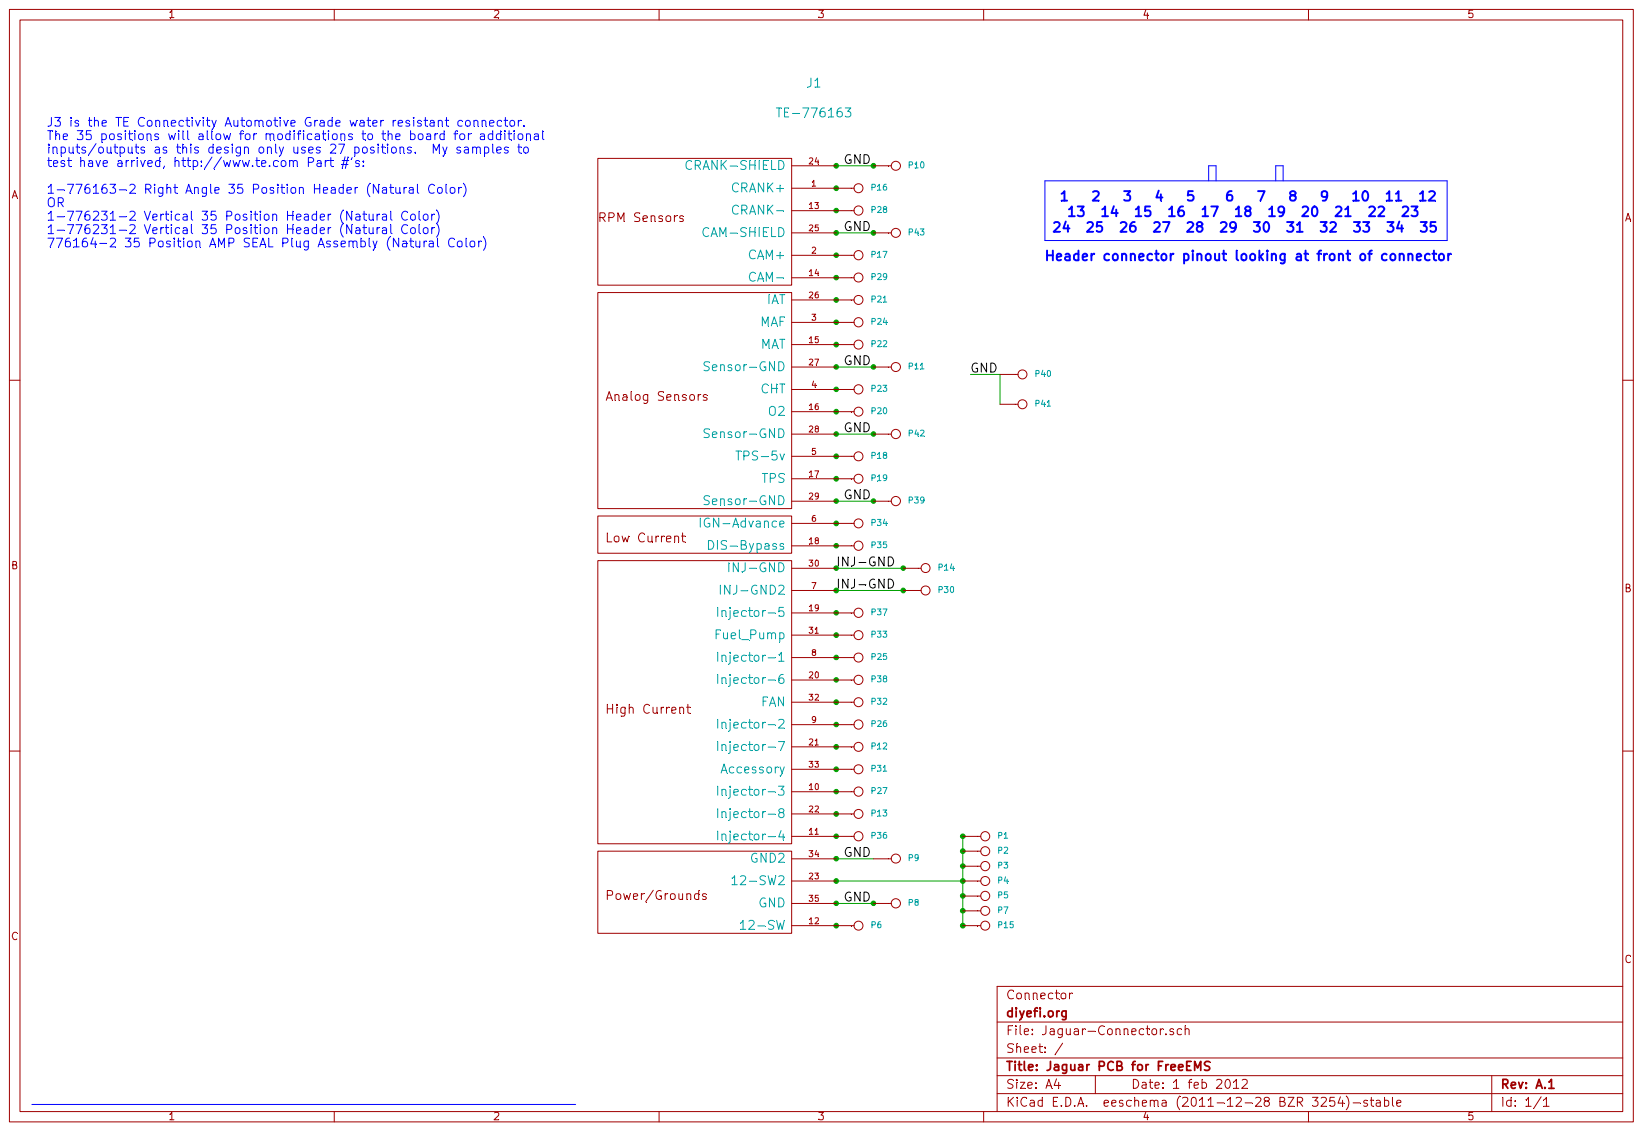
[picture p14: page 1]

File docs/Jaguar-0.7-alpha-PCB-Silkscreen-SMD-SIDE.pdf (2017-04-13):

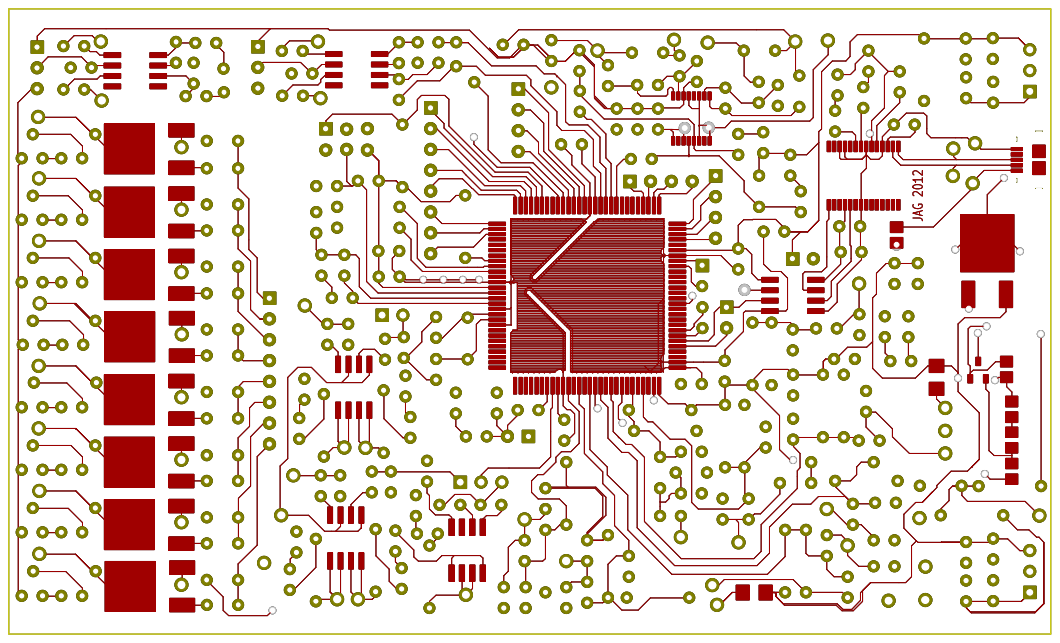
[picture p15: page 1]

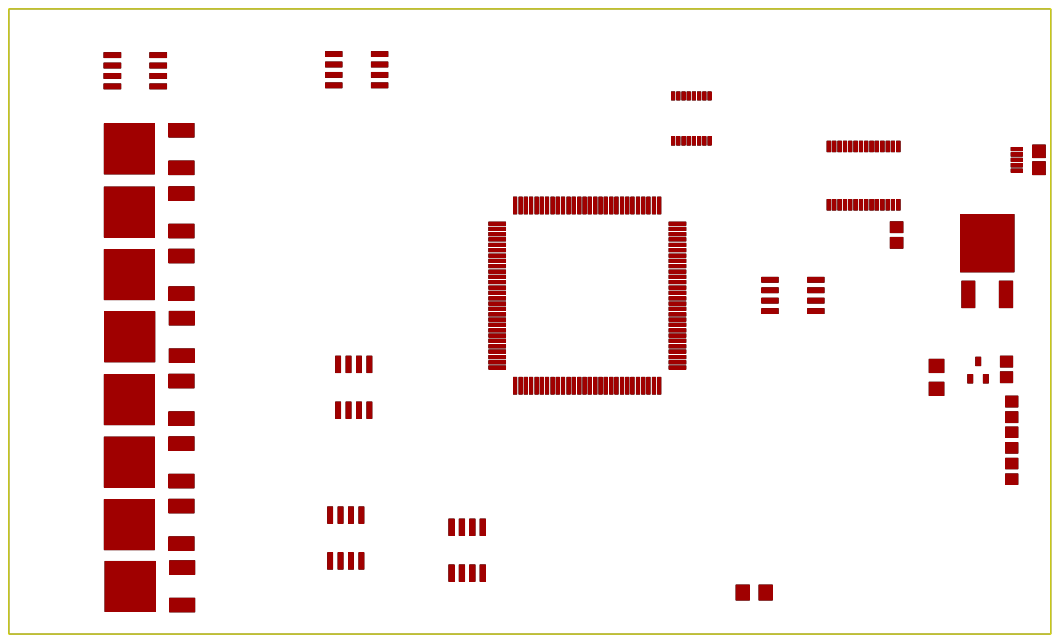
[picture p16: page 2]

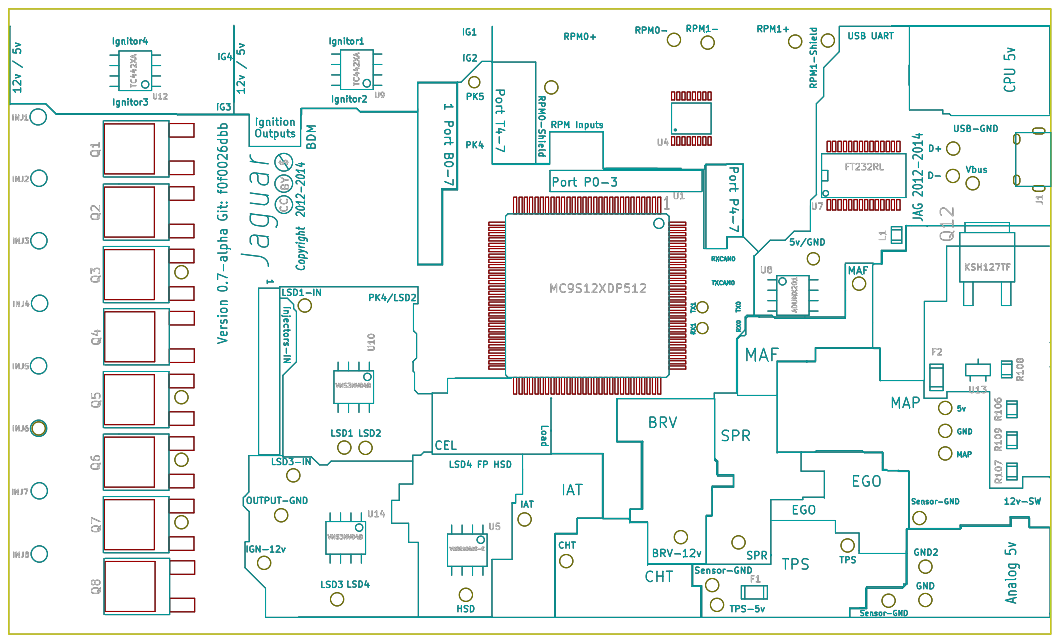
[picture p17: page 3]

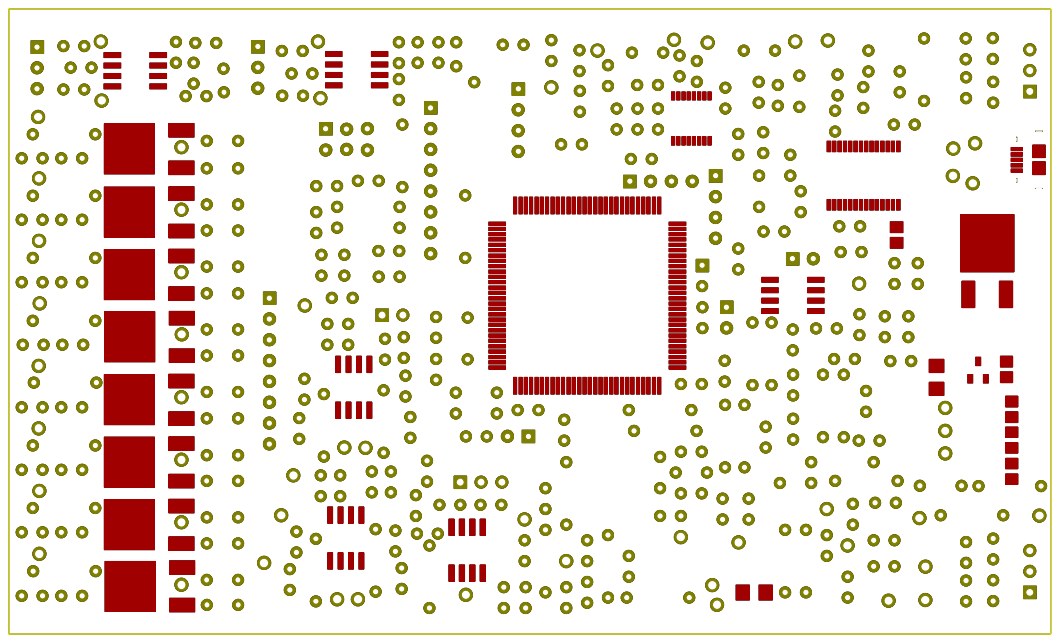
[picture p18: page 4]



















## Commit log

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2012-01-20 Redesigned schematics and board
    [$savepcb.brd, FreeRouter.dsn, Injectors.sch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]
2012-01-21 deleted: Injectors.bak modified: Jaguar-Schematic.pdf deleted: Jaguar-cache.bak deleted: Jaguar.bak modified: Jaguar.lst modified: Jaguar.ods modified: Jaguar.pro deleted: Older/Jaguar-Schematic.pdf 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
    [Jaguar.brd, Jaguar.dsn, Jaguar.ods]
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2012-01-23 Modified: schematics to correct errors
    [Injectors.sch, Jaguar.sch, Outputs.sch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]
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2012-01-23 Fix MAX9926 Configuration and created new PCB and PDF
    [Injectors.sch, Jaguar.brd, Jaguar.sch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]
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2012-01-27 Load/Run Circuit FIXED, Update BOM, PDFs, PNGs
    [$savepcb.brd, Injectors.sch, Jaguar.brd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]
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2012-02-05 Added Jaguar.lib to share KiCAD library, updated schematic files for this library
    [Injectors.sch, Jaguar.sch, Outputs.sch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]
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2012-02-05 Corrected PCB files
    [Jaguar.brd]
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2012-02-07 Updated all files to show locked at Revision A.2 for prototype etching
    [$savepcb.brd, Jaguar.brd, Jaguar.ods]
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2012-02-09 Updated PCB files and PNGs, added GND reliefs under CPU and text on SMD side of PCB
    [Jaguar.brd]
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2012-03-07 pcb/Jaguar.brd changed to correct the R12/C1 pad errors.
    [$savepcb.brd, Jaguar.brd, Jaguar.ods]
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2012-05-14 Updated TODO.md with new suggestions and added git hash to Jaguar.brd under Rev. AG
    [$savepcb.brd, Jaguar.brd]
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2012-05-14 Corrected MCU part number in docs/Jaguar.ods
    [Jaguar.ods]
2012-05-14 Corrected C10/C11 information (20pF) docs/Jaguar.ods
    [Jaguar.ods]
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2012-05-27 Deleted D3 Zener diode at the output of the 5vdc-cpu regulator as the MCU shouldn't feed voltage back to the regulator
    [Injectors.sch, Jaguar.sch, Outputs.sch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]
2012-05-27 Added 1k current limiting resistors between MAX9926 outputs and MCU T0/T1 inputs
    [Injectors.sch, Jaguar.sch, Outputs.sch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]
2012-05-27 Change 5vdc-analog to 5vdc-cpu at CEL (D1) so that the CPU supply is used to power up all the necessary MCU functions. (Analog supply should only be for inputs from the engine)
    [Injectors.sch, Jaguar.sch, Outputs.sch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]
2012-05-27 C10 and C11 (crystal load capacitors) changed to 20pF to match the manufacturer specifications.
    [Injectors.sch, Jaguar.sch, Outputs.sch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]
2012-05-27 Started updating PCB, changed to SMD XOR chip, deleted R62 across crystal, added one of the 1k resistors on the output of the MAX9926 chip
    [Injectors.sch, Jaguar.brd, Jaguar.sch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]
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2012-05-27 Updated README.md to warn people not to use the PCB files to create boards since I am in the middle of making corrections to the PCB layout.
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2012-07-02 updated docs/Jaguar.ods to remove D43, D44, updated U5 to SMD component,Added R80/R81 to MAX9926 outputs
    [Jaguar.ods]
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2012-07-03 Updated git commit hash on PCB to ce851f0c10bfdb370ea6bbc7158e06a5837e0ac7 after Injector Output/LED circuit changes
    [Jaguar.brd]
2012-07-04 Continuing to update component solder pad sizes and modified trace sizes according to current handling capacity
    [Injectors.sch, Jaguar.brd, Jaguar.sch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]
2012-07-04 Pads all correct size now, still need to replace LEDs with new footprint with Anode clearly marked
    [Jaguar.brd]
2012-07-04 All LEDs replaced with new footprint with Anode marked
    [Jaguar.brd]
2012-07-04 Moved BDM connector to allow for room around it for easier cable connection
    [Injectors.sch, Jaguar.brd, Jaguar.sch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]
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2012-07-05 Corrected power feed to MAX9926 decouple capacitors to make sure power feed is on the correct side
    [Jaguar.brd]
2012-07-05 Moved FTDI USB IC decouple capacitors closer to IC and re-routed power feed to the decouple capacitors
    [Jaguar.brd]
2012-07-05 Label GND/RESET/+5v next to BDM outline
    [Jaguar.brd]
2012-07-05 Corrected power feed to MAP decoupling capacitors
    [Jaguar.brd]
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2012-07-05 C26, C42 and C43 in the MAX9926 circuit changed from 6mm disc capacitors to 3mm disc capacitors
    [Jaguar.brd]
2012-07-05 Regenerated PCB file after changing C26, C42 and C43 from 6mm to 3mm disc capacitors
    [Jaguar.brd]
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2012-07-05 Re-routed some connections on the PCB, the LED illumination 12v supplies to the outputs didn't warrant separate connection points
    [Injectors.sch, Jaguar.brd, Jaguar.sch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]
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2012-07-06 Added additional wire connection points for 1 ground connection per Injector MOSFET and increased the size of the trace to these pads
    [Injectors.sch, Jaguar.brd, Jaguar.sch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]
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2012-07-06 Added D43 and D44 back to the schematic and to the board
    [Jaguar.brd]
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2012-07-07 Changed smallest traces from 0.0070" to 0.0124" except for the Mini USB traces
    [Jaguar.brd]
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2012-07-07 Moved the MOSFET ground wire connectors and the MOSFET input resistors to be symmetrical
    [Jaguar.brd]
2012-07-07 Updated git hash on PCB to ee554bf (shortening it to 7 characters and larger font to make it easier to read)
    [Jaguar.brd]
2012-07-07 Updated git hash on PCB to read "git: 03bc5afbb5" (as a permanent part of the front side silkscreen layer)
    [Jaguar.brd]
2012-07-08 Connected all Injector MOSFET ground connection points together, added PNP transistor, removed HCPL optocoupler ICs
    [Injectors.sch, Jaguar.brd, Jaguar.sch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]
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2012-07-08 Changed Injector MOSFET grounds to be in pairs with a 0.0700" trace between them instead of a 0.0350" trace like the Injector outputs have
    [Injectors.sch, Jaguar.brd, Jaguar.sch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]
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2012-08-09 Added C49, C51, D45, D46 and R82 for MAF input filtering and protection of MCU pin 72.
    [Injectors.sch, Jaguar-Connector.brd, Jaguar.brd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]
2012-08-09 Updated git hash to 2559b09420 on PCB to mark the addition of the components for the MAF input.
    [Jaguar.brd]
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2012-08-30 Added MAF input protection circuit to TODO.md so it doesn't get forgotten.
2012-09-18 Removed PNP modification and added ADUMx201 Digital Isolator between FTDI and MCU
    [Injectors.sch, Jaguar.brd, Jaguar.ods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]
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2012-09-22 Added RX/TX and RX1/TX1 solder pads at MCU for future serial datalogging experimentation
    [Injectors.sch, Jaguar.brd, Jaguar.sch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]
2012-09-22 Updated git hash to 5b07551b79 marking the addition of the RX/TX and RX1/TX1 solder pads
    [Jaguar.brd]
2012-09-23 Changed CRANK references to RPM0, changed CAM references to RPM1, added PK4 and PK5 solder pads.
    [Injectors.sch, Jaguar.brd, Jaguar.sch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]
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2012-09-23 Updated X-OR part number on BOM and PCB to 24mA rated outputs IC
    [Jaguar.brd, Jaguar.ods]
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2012-09-24 Added MAP sensor solder pad labels (5v, GND, MAP) to silk screen on SMD side so users will know which pads to connect external MAP sensor wiring to.
    [Jaguar.brd, Jaguar.ods]
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2012-09-24 Added D47 and D48 input protection diodes to MAP circuit if the user wishes to use an external MAP sensor
    [Injectors.sch, Jaguar.brd, Jaguar.sch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]
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2012-10-23 Corrected MAX9926 input circuits with 1k on IN+ and IN- inputs, Added 1k/1k 2.5vdv voltage divider to IN- inputs based on Dan's testing.
    [Injectors.sch, Jaguar.sch, Outputs.sch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]
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2012-11-10 Board layout changed to place the TC442xA ICs, replaced the MAP sensor with SMD version and added AAP SMD sensor.
    [Injectors.sch, Jaguar.brd, Jaguar.sch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]
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2013-04-08 Corrected AAP and MAP pinouts and traces. Changed version to 0.5-alpha.
    [Injectors.sch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]
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2013-04-26 Updated TODO.md with things I noticed on 0.4-alpha board while building the first PCB. Also updated BOM to replace discontinued components.
    [Jaguar.ods]
2013-04-26 Updated TODO.md to remove R79 from the BOM, it has been replaced by L1.
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2013-05-10 Corrected silkscreen labels for over voltage protection SMD components.
    [Jaguar.brd]
2013-05-10 Corrected L1 silkscreen so it can be read.
    [Jaguar.brd]
2013-05-10 Updated TODO.md after correcting SMD component silkscreen labels.
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2013-05-10 Deleted D2 from the PCB as it is no longer in the schematic.
    [Jaguar.brd]
2013-05-10 IAT silkscreen lettering on component side read TAT, moved IAT away from pad to correct.
    [Jaguar.brd]
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2013-05-10 * 12v trace to MOV was too narrow and would burn while MOV active, made trace wider.
    [Jaguar.brd]
2013-05-10 Added mica isolator kits to the TODO.md list as they were missing on the BOM.
2013-05-10 RPM0 and RPM1 LED silkscreen labels were reversed.
    [Jaguar.brd]
2013-05-11 Low side driver diodes were not labeled correctly, it had partial part number rather than component ID. Changed Load/Run label to Load.
    [Jaguar.brd, Jaguar.ods]
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2013-05-12 Updated TODO.md for R20 and R23 footprint error.
    [Injectors.sch, Jaguar.ods, Jaguar.sch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]
2013-05-13 R20 and R23 footprints were too small for 3w resistor, used bigger footprint and moved other components out of the way.
    [Jaguar.brd]
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2013-05-21 Changed Load pads to use a 0.0315" drill like the BDM pads for a snug fit so the header doesn't fall out.
    [Jaguar.brd]
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2013-06-09 Added note on the Outputs schematic that reads "TC4426A has two inverting drivers, while the TC4427A has two non-inverting drivers, the TC4428A has one inverting and one non-inverting driver."
    [Injectors.sch, Jaguar.sch, Outputs.sch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]
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2013-07-19 Added note about known missing component IDs on the first sheet of the schematic. Also labeled schematic and PCB as 0.6-alpha-RC1.
    [Injectors.sch, Jaguar.brd, Jaguar.sch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]
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2013-07-19 Updated TODO.md to show that the missing component IDs have been identified on the schematic.
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2013-08-18 Corrected weird 5v-analog trace near F1 that johntramp noticed. :)
    [Jaguar.brd]
2013-08-26 Corrected footprints for the adjustable zener (U13) and the PNP transistor (Q12) as they are numbered differently by the manufacturer compared to the KiCAD footprints for SOT-23-3 and SOT-223 compone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
    [Jaguar.brd]
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2013-09-15 Corrected ground plane net name so that the ground plane was connected to GND.
    [Jaguar.brd]
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
